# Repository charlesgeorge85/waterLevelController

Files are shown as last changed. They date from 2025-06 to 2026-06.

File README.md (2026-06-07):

# Water Level Controller for Home

This project implements a smart water tank pump controller using an ESP32 microcontroller. It manages the transfer of water between an Underground Tank (UGT) and an Overhead Tank (OHT), ensuring safe, efficient operation with dry-run protection and a web interface for monitoring and manual control.

## 1. Problem Statement

The system is designed to automatically control a water pump to transfer water from a UGT to an OHT. Key challenges addressed include:

- Preventing pump operation when UGT is empty (dry run).
- Automating pump ON/OFF based on OHT and UGT water levels.
- Providing manual mode, switch is set to manual, in manual mode, pump will be 'on', so thts pump can be controlled via main power switch

## 1.1 Tank Level Thresholds

- **Overhead Tank (OHT):**
  - `OHT_FULL`: Tank is full.
  - `OHT_EMPTY`: Tank is empty.

- **Underground Tank (UGT):**
  - `UGT_EMPTY`: Tank is empty.
  - `UGT_NOT_EMPTY`: Tank has sufficient water.

## 2. Use Cases

### 2.1 Pump Activation

The pump is activated when:
- OHT level is below `OHT_EMPTY`.
- UGT level is above `UGT_EMPTY`.

### 2.2 Pump Deactivation

The pump is turned off when:
- OHT reaches `OHT_FULL`, or
- UGT falls below `UGT_EMPTY`, or
- A dry-run condition is detected.

If deactivation is due to UGT low level, the pump will only reactivate once UGT is above `UGT_NOT_EMPTY`.

### 2.3 Dry Run Detection & Handling

- Dry-run is detected via motor current using a Current Transformer (CT).
- For a 0.25 HP motor, current < 0.8 A indicates a dry run, during normal run, the measured current is 1.27A
- On dry run:
  - A buzzer alerts.
  - Alarm can be cleared with a Alarm reset switch
  
## 3. Hardware Implementation

- **Controller**: ESP32
- **Features**:
  - Water level monitoring (UGT & OHT)
  - Motor control (auto/manual)
  - Current sensing
  - Configurable dry-run threshold
  - Web UI for (future Plan):
    - Displaying water levels
    - Manual motor control
    - Viewing current consumption
    - Threshold configuration

## 4. Web UI(future Plan)

A web-based interface hosted on ESP32 allows real-time visualization and control of the pump system.

## 5. ESP32 Devkit V1 details

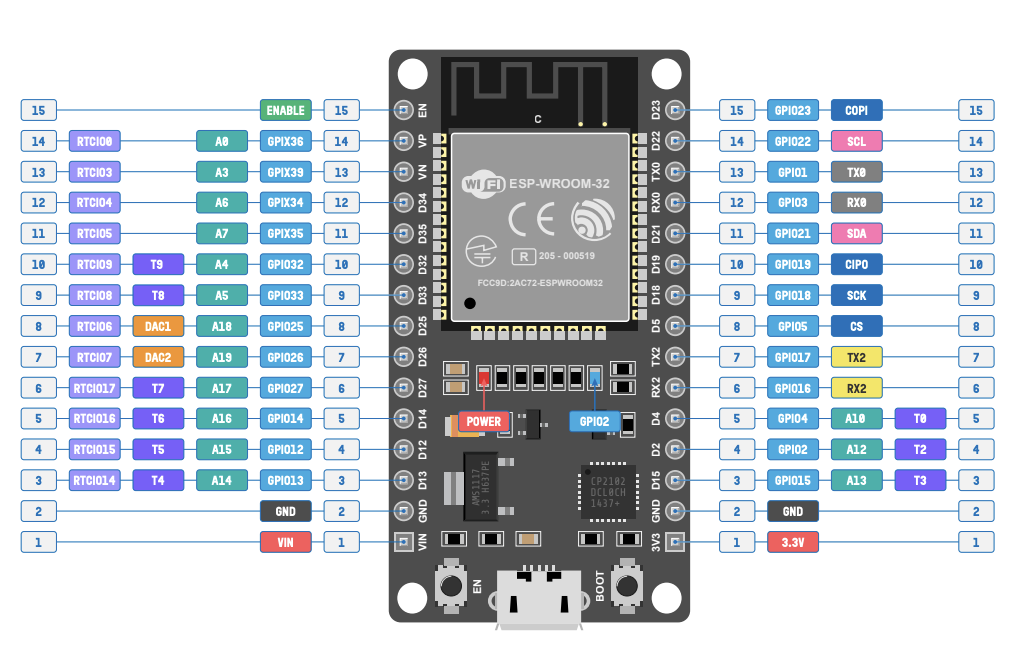
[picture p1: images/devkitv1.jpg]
ESP32 Pinout


[ESP32 DOIT DevKit V1 Board Details](https://www.espboards.dev/esp32/esp32doit-devkit-v1/)

---

### Author
Joseph George

### License
This project is open-source and available under the [MIT License](LICENSE).

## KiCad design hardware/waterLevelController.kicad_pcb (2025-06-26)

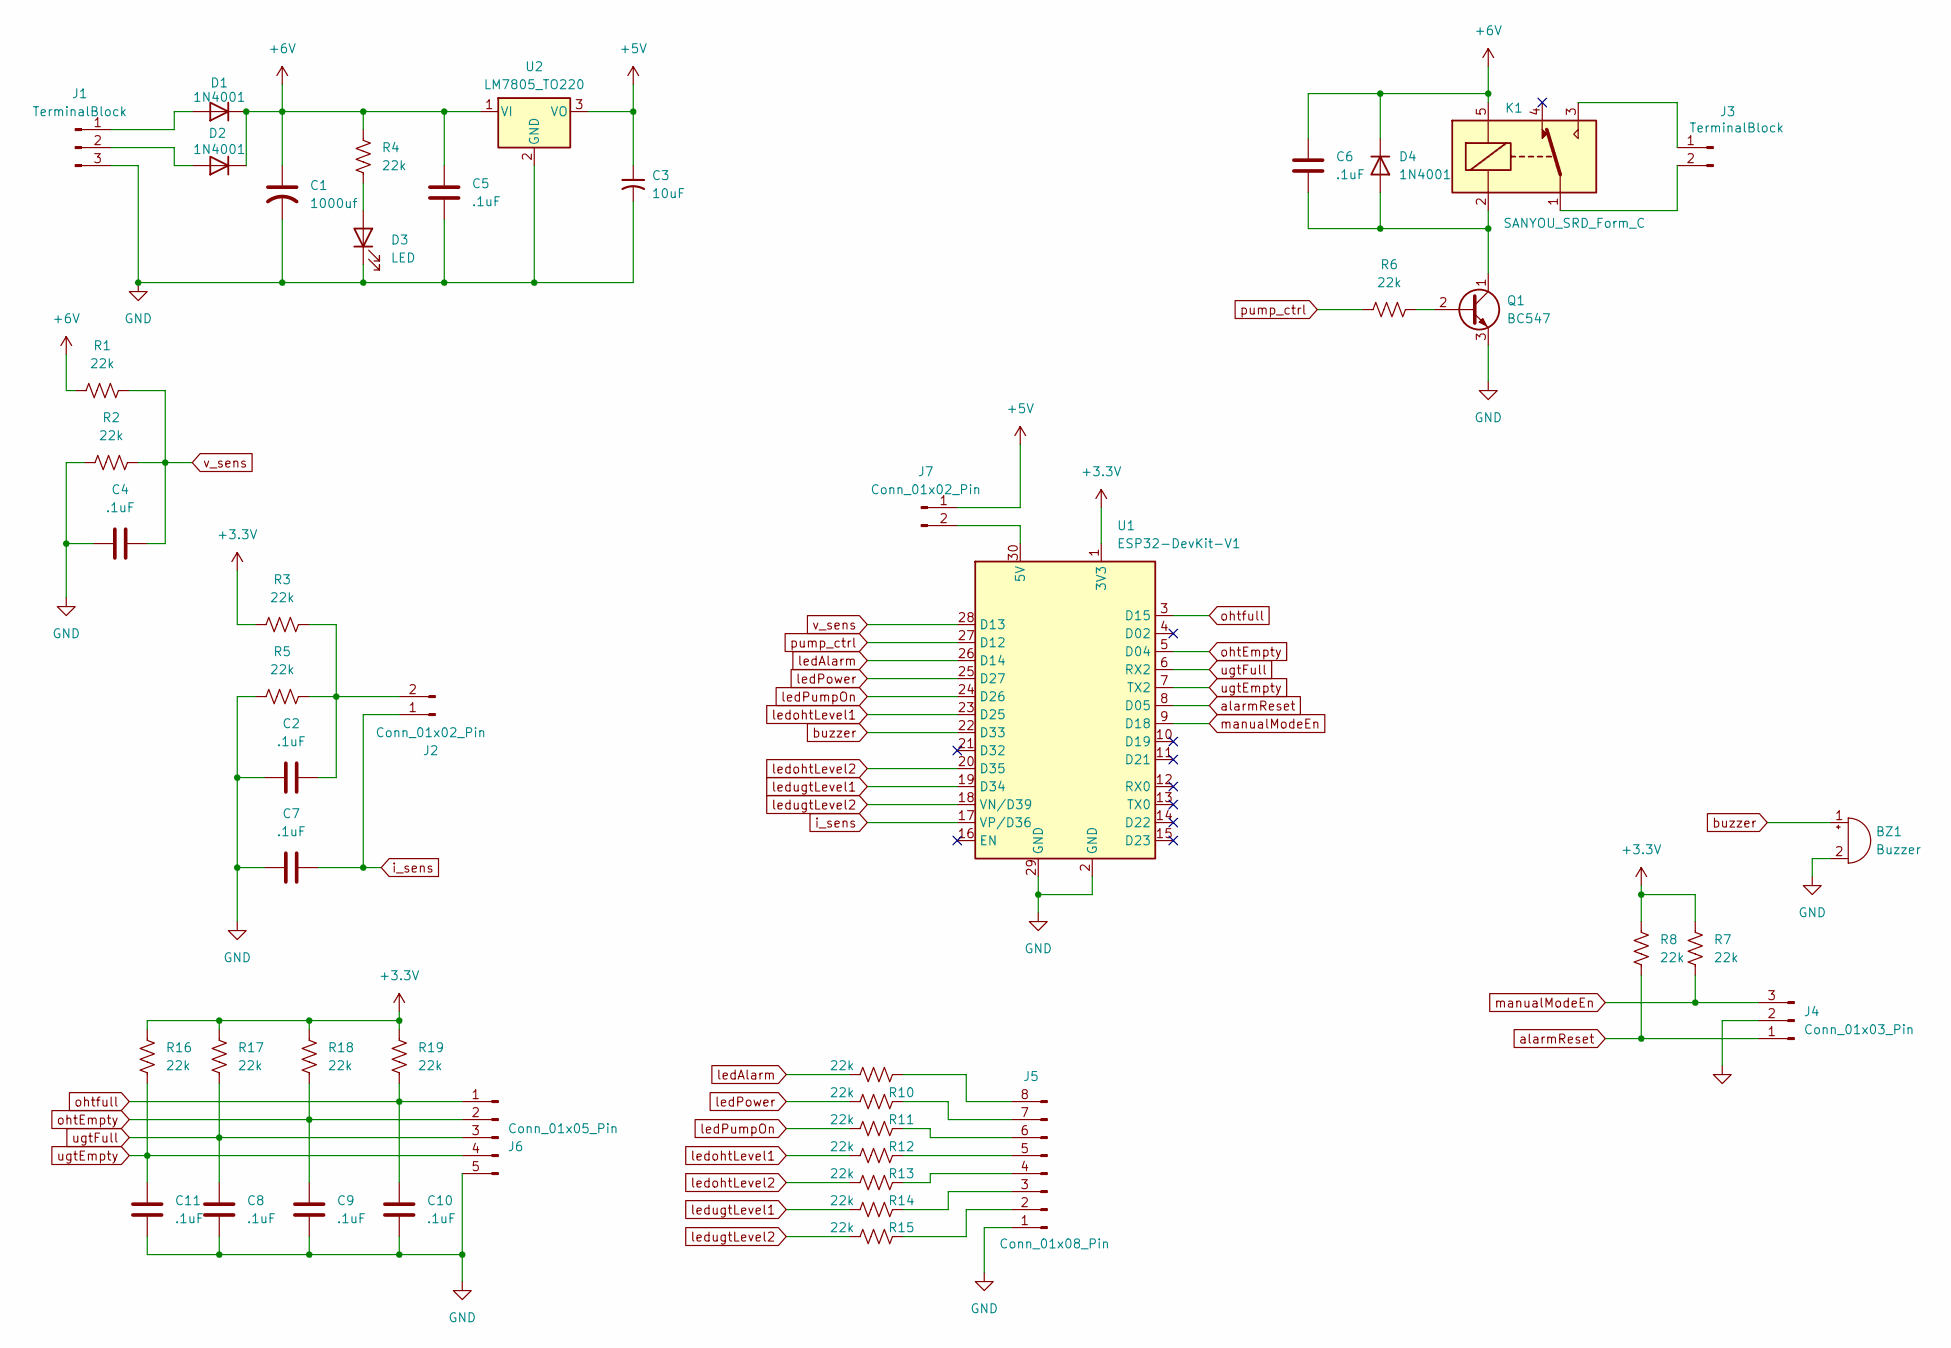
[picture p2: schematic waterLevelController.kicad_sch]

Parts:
BZ1: Buzzer; BUZ_12X7P6
C1: 1000uf; C_Radial_D12.5mm_H20.0mm_P5.00mm
C2, C4, C5, C6, C7, C8, C9, C10, C11: .1uF; C_Disc_D3.8mm_W2.6mm_P2.50mm
C3: 10uF; CP_Radial_D8.0mm_P2.50mm
D1, D2, D4: 1N4001; D_DO-41_SOD81_P10.16mm_Horizontal
D3: LED; LED_D3.0mm
J1: TerminalBlock; PhoenixContact_MCV_1,5_3-G-3.81_1x03_P3.81mm_Vertical
J2, J7: Conn_01x02_Pin; PinHeader_1x02_P2.54mm_Vertical
J3: TerminalBlock; PhoenixContact_MCV_1,5_2-G-3.81_1x02_P3.81mm_Vertical
J4: Conn_01x03_Pin; PinHeader_1x03_P2.54mm_Vertical
J5: Conn_01x08_Pin; PinHeader_1x08_P2.54mm_Vertical
J6: Conn_01x05_Pin; PhoenixContact_MCV_1,5_5-G-3.81_1x05_P3.81mm_Vertical
K1: SANYOU_SRD_Form_C; Relay_SPDT_SANYOU_SRD_Series_Form_C
Q1: BC547; TO-92_Wide
R1, R2, R3, R4, R5, R6, R7, R8, R9, R10, R11, R12, R13, R14, R15, R16, R17, R18, R19: 22k; R_Axial_DIN0309_L9.0mm_D3.2mm_P5.08mm_Vertical
U1: ESP32-DevKit-V1
U2: LM7805_TO220; TO-220-3_Vertical

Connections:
+3.3V: R3.1, R7.2, R8.2, R16.1, R17.1, R18.1, R19.1, U1.1 (3V3)
+5V: C3.1, J7.1, U2.3 (VO)
+6V: C1.1, C5.2, C6.2, D1.1 (K), D2.1 (K), D4.1 (K), K1.5, R1.1, R4.1, U2.1 (VI)
GND: BZ1.2 (-), C1.2, C2.1, C3.2, C4.1, C5.1, C7.1, C8.2, C9.2, C10.2, C11.2, D3.1 (K), J1.3, J4.2, J5.1, J6.5, Q1.3 (E), R2.1, R5.1, U1.2 (GND), U1.29 (GND), U2.2 (GND)
unnamed: D1.2 (A), J1.1
unnamed: D2.2 (A), J1.2
unnamed: D3.2 (A), R4.2
unnamed: C6.1, D4.2 (A), K1.2, Q1.1 (C)
unnamed: C2.2, J2.2, R3.2, R5.2
unnamed: J3.1, K1.3
unnamed: J3.2, K1.1
unnamed: J5.2, R15.1
unnamed: J5.3, R14.1
unnamed: J5.4, R13.1
unnamed: J5.5, R12.1
unnamed: J5.6, R11.1
unnamed: J5.7, R10.1
unnamed: J5.8, R9.1
unnamed: J7.2, U1.30 (5V)
unnamed: Q1.2 (B), R6.2
alarmReset: J4.1, R8.1, U1.8 (D05)
buzzer: BZ1.1 (+), U1.22 (D33)
i_sens: C7.2, J2.1, U1.17 (VP/D36)
ledAlarm: R9.2, U1.26 (D14)
ledPower: R10.2, U1.25 (D27)
ledPumpOn: R11.2, U1.24 (D26)
ledohtLevel1: R12.2, U1.23 (D25)
ledohtLevel2: R13.2, U1.20 (D35)
ledugtLevel1: R14.2, U1.19 (D34)
ledugtLevel2: R15.2, U1.18 (VN/D39)
manualModeEn: J4.3, R7.1, U1.9 (D18)
ohtEmpty: C9.1, J6.2, R18.2, U1.5 (D04)
ohtfull: C10.1, J6.1, R19.2, U1.3 (D15)
pump_ctrl: R6.1, U1.27 (D12)
ugtEmpty: C11.1, J6.4, R16.2, U1.7 (TX2)
ugtFull: C8.1, J6.3, R17.2, U1.6 (RX2)
v_sens: C4.2, R1.2, R2.2, U1.28 (D13)

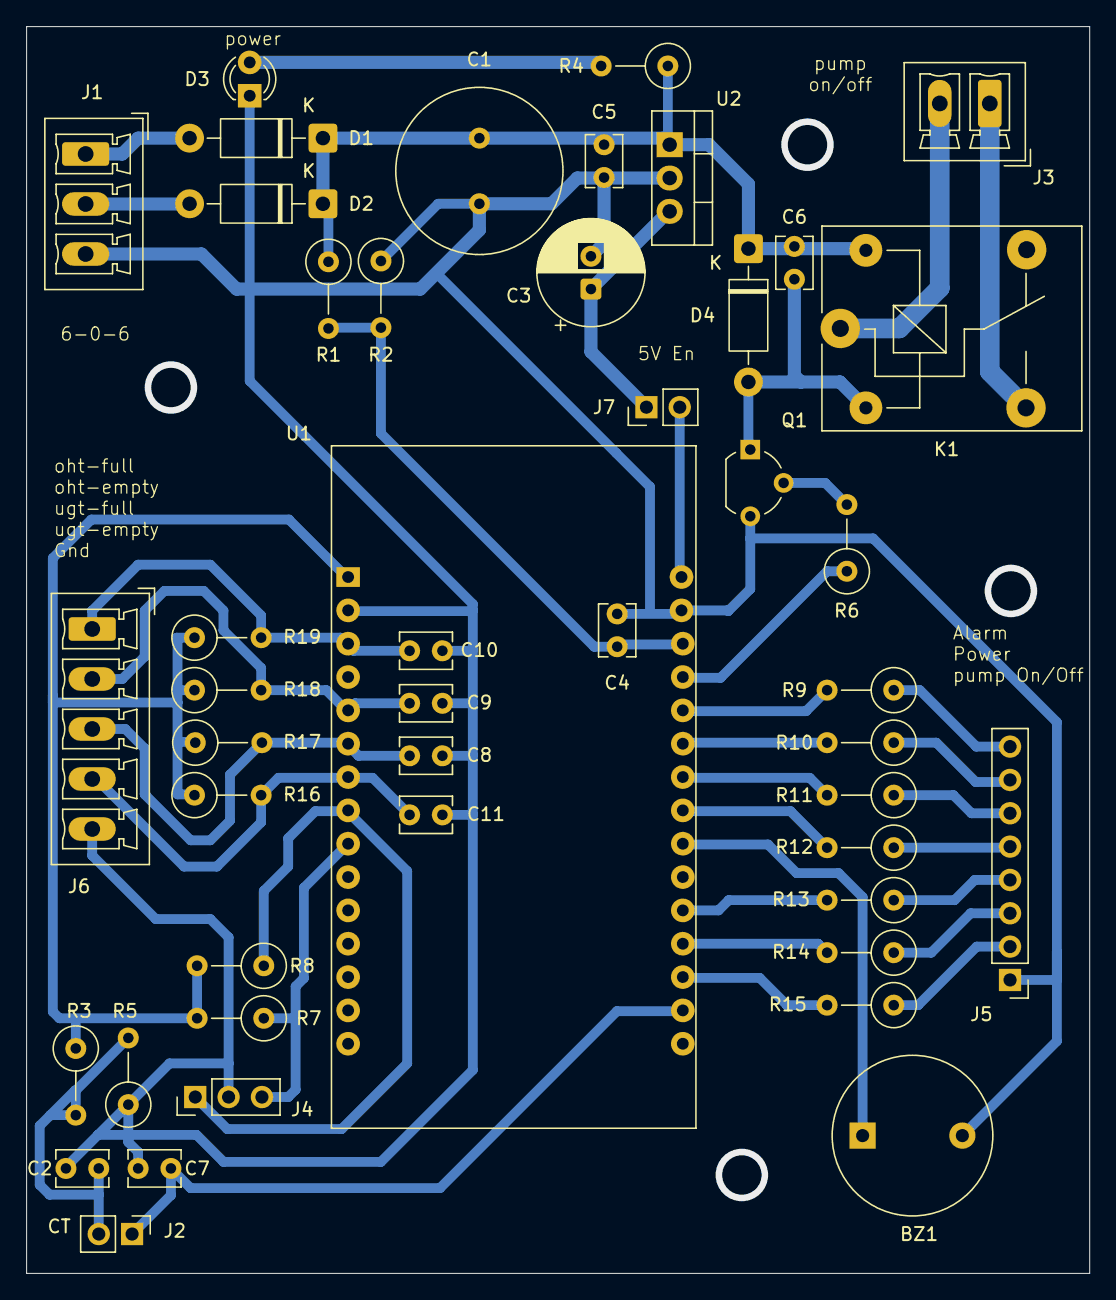
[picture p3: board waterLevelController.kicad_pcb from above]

Board: 2 copper layers, 81.0 x 95.0 mm, 46 parts (0 on the bottom side), 37 nets.

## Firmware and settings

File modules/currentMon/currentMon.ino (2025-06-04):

#define ADC_PIN 36          // ESP32 ADC pin (GPIO36 = ADC1_CH0)
#define VREF 3.3            // ADC reference voltage
#define ADC_RES 4095        // 12-bit ADC
#define VOLTAGE_BIAS 1.580  // Measured midpoint voltage (bias)
#define SENSOR_SENSITIVITY 0.1  // 0.1 V/A (for SCT-013-010)
#define SAMPLE_DURATION 200  // Sampling time in milliseconds (for 10 cycles at 50Hz)

void setup() {
  Serial.begin(115200);
  analogReadResolution(12);  // ESP32 default is 12-bit
}

void loop() {
  unsigned long i_sam_start_time = millis();
  float sum_squared = 0;
  int sample_count = 0;

  while ((millis() - i_sam_start_time) < SAMPLE_DURATION) {
    int adc_val = analogRead(ADC_PIN);
    float voltage = (adc_val * VREF) / ADC_RES;
    float ac_component = voltage - VOLTAGE_BIAS;

    sum_squared += ac_component * ac_component;
    sample_count++;

    delayMicroseconds(200); // ~5 kHz sampling
  }

  // Calculate RMS voltage
  float mean_squared = sum_squared / sample_count;
  float rms_voltage = sqrt(mean_squared);

  // Convert to current using sensor sensitivity
  float rms_current = rms_voltage / SENSOR_SENSITIVITY;

  //scaling Correction, bu board 
  rms_current *= 0.258/3.34;

  Serial.print("RMS Current = ");
  Serial.print(rms_current, 3);
  Serial.println(" A");

  delay(1000); // Wait before next reading
}

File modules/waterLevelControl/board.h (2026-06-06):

#ifndef BOARD_H
#define BOARD_H

// GPIO Pin Definitions
#define OHT_FULL_PIN        15
#define OHT_EMPTY_PIN       04
#define UGT_NOT_EMPTY_PIN   16
#define UGT_EMPTY_PIN       17

#define ALARM_CLEAR_PIN     05
#define MANUAL_MODE_SWITCH  18

#define PUMP_CONTROL_PIN    32
#define PUMP_LED_PIN        02
#define BUZZER_PIN          33

// Status LEDs
#define LED_ALRM_PIN        27
#define LED_PUMP_PIN        26
#define LED_PWR_PIN         14

// ADC Parameters
#define VREF 3.3
#define ADC_RES 4095

// Current sense
#define CT_SENS_PIN 36

#define VOLTAGE_BIAS 1.580
#define SENSOR_SENSITIVITY 0.1
#define SAMPLE_DURATION 200

// Dry-run thresholds
#define DRY_RUN_CURRENT_THRESHOLD   0.8
#define DRY_RUN_RECOVERY_THRESHOLD  2.5

// Voltage Sense
#define VAC_SENS_ADC_PIN 13

// Dry-run delay before checking (after pump ON)
const unsigned long DRY_RUN_DELAY_MS = 0.5 * 60 * 1000;
const unsigned long DRY_RUN_BUZZ_INTERVAL = 30 * 60 * 1000;

#endif

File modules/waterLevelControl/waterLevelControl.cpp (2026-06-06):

#include <Arduino.h>
#include "board.h"

// System States
bool toggle = false;
bool pumpOn = false;
bool manualMode = false;
bool dryRunDetected = false;
bool ugtPreviouslyEmpty = false;
bool ohtPreviouslyEmpty = false;

unsigned long lastDryRunBuzzTime = 0;
unsigned long pumpStartTime = 0;

void setup() {
  Serial.begin(115200);
  analogReadResolution(12);  // ESP32 default is 12-bit
  
  // Sensor Inputs
  pinMode(OHT_FULL_PIN, INPUT);
  pinMode(OHT_EMPTY_PIN, INPUT);
  pinMode(UGT_EMPTY_PIN, INPUT);
  pinMode(UGT_NOT_EMPTY_PIN, INPUT);

  // Control Outputs
  pinMode(PUMP_CONTROL_PIN, OUTPUT);
  pinMode(PUMP_LED_PIN, OUTPUT);
  pinMode(BUZZER_PIN, OUTPUT);

  pinMode(LED_ALRM_PIN, OUTPUT);
  pinMode(LED_PUMP_PIN, OUTPUT);
  pinMode(LED_PWR_PIN, OUTPUT);

  // User Inputs
  pinMode(ALARM_CLEAR_PIN, INPUT_PULLUP);
  pinMode(MANUAL_MODE_SWITCH, INPUT_PULLUP);

  digitalWrite(PUMP_CONTROL_PIN, LOW);
  digitalWrite(PUMP_LED_PIN, LOW);
  digitalWrite(BUZZER_PIN, LOW);
  
  digitalWrite(LED_ALRM_PIN, LOW);
  digitalWrite(LED_PUMP_PIN, LOW);
  digitalWrite(LED_PWR_PIN, LOW);


}

bool readSensor(int pin) {
  return digitalRead(pin) == LOW; // Assume LOW means "active"
}

void activatePump() {
  if (!pumpOn) {
    digitalWrite(PUMP_CONTROL_PIN, HIGH);
    digitalWrite(PUMP_LED_PIN, HIGH);
    digitalWrite(LED_PUMP_PIN, HIGH);
    pumpOn = true;
    pumpStartTime = millis();
    tone(BUZZER_PIN, 440, 300); // 300 ms sec beep @440Hz
    Serial.println("Pump ON");
  }
}

void deactivatePump() {
  if (pumpOn) {
    digitalWrite(PUMP_CONTROL_PIN, LOW);
    digitalWrite(PUMP_LED_PIN, LOW);
    digitalWrite(LED_PUMP_PIN, LOW);
    pumpOn = false;
    Serial.println("Pump OFF");
    tone(BUZZER_PIN, 2000, 200); // 300 ms sec beep @440Hz
    
  }
}

void handleDryRun(float current) {
  if (!pumpOn and !dryRunDetected) return; // ✅ Only check if pump is running

  unsigned long now = millis();
  if (now - pumpStartTime < DRY_RUN_DELAY_MS) {
    // ✅ Wait 2 minutes before checking
    return;
  }
   Serial.println("Dry run check initiated...");
 
 if (current < DRY_RUN_CURRENT_THRESHOLD) {
      dryRunDetected = true;
      deactivatePump();
      Serial.println("Dry run detected.....");
    }

  if (dryRunDetected) {
    
      tone(BUZZER_PIN, 1000, 100); // 0.1 sec beep @ 1KHz
      digitalWrite(LED_ALRM_PIN, toggle);
    

    if (digitalRead(ALARM_CLEAR_PIN) == LOW) {
      dryRunDetected = false;
      Serial.println("Dry-run alarm cleared.");
      digitalWrite(LED_ALRM_PIN, LOW);
    }
  }
}


float voltMon()
{
 // Voltage Sampling
  int adc_val = analogRead(VAC_SENS_ADC_PIN); // 0 to 4095
  float voltageSense = (adc_val / 4095.0) * 3.3; // Convert to volts
  //scaling correction by board measurement
  float voltMains = 242*voltageSense/2.98;
  return voltMains;
}

float currentMon()
{
  // Current Sampling
  unsigned long i_sam_start_time = millis();
  float sum_squared = 0;
  int sample_count = 0;

  while ((millis() - i_sam_start_time) < SAMPLE_DURATION) {
    int adc_val = analogRead(CT_SENS_PIN);
    float voltage = (adc_val * VREF) / ADC_RES;
    float ac_component = voltage - VOLTAGE_BIAS;

    sum_squared += ac_component * ac_component;
    sample_count++;

    delayMicroseconds(200); // ~5 kHz sampling
  }

  // Calculate RMS voltage
  float mean_squared = sum_squared / sample_count;
  float rms_voltage = sqrt(mean_squared);

  // Convert to current using sensor sensitivity
  float rms_current = rms_voltage / SENSOR_SENSITIVITY;

  //scaling Correction, bu board 
  rms_current *= 0.258/3.34;

  return(rms_current);
}

void loop() {
  
  float rms_current = currentMon();
  float rms_voltage = voltMon();
  float power = rms_voltage * rms_current;
  
  /*
  Serial.print("RMS Current = ");
  Serial.print(rms_current, 3);
  Serial.println(" A");
  
  Serial.print("Vrms = ");
  Serial.print(rms_voltage, 3);
  Serial.println(" V");

  Serial.print("Power = ");
  Serial.print(power, 3);
  Serial.println(" Watts");
*/
  manualMode = digitalRead(MANUAL_MODE_SWITCH) == LOW;
  toggle = !toggle;

  
  //digitalWrite(LED_ALRM_PIN, toggle);
  digitalWrite(LED_PWR_PIN, HIGH);
  
  if (manualMode) {
    Serial.println("Manual Mode Active");
    // Optionally handle pump ON/OFF via buttons here
    activatePump();
  } else {
    
    // Read tank sensor states
    bool ohtEmpty = digitalRead(OHT_EMPTY_PIN) == HIGH;
    bool ohtFull = digitalRead(OHT_FULL_PIN) == LOW;
    bool ugtEmpty = digitalRead(UGT_EMPTY_PIN) == HIGH;
    bool ugtNotEmpty = digitalRead(UGT_NOT_EMPTY_PIN) == LOW;
/*
    Serial.printf("ohtEmpty: %s\n", ohtEmpty ? "true" : "false");  // Outputs: Status: true
    Serial.printf("ohtFull: %s\n", ohtFull ? "true" : "false");  // Outputs: Status: true
    Serial.printf("ugtEmpty: %s\n", ugtEmpty ? "true" : "false");  // Outputs: Status: true
    Serial.printf("ugtNotEmpty: %s\n", ugtNotEmpty ? "true" : "false");  // Outputs: Status: true
*/
    // Track UGT history
    if (ugtEmpty) {
      ugtPreviouslyEmpty = true;
      deactivatePump(); // Safety: prevent dry run
    }

    if (ugtPreviouslyEmpty && ugtNotEmpty && !ugtEmpty) {
      ugtPreviouslyEmpty = false; // Reset lock
    }

    // Track OHT History

    if (ohtEmpty) {
      ohtPreviouslyEmpty = true;
    }

    if (ohtPreviouslyEmpty && ohtFull && !ohtEmpty) {
      ohtPreviouslyEmpty = false; // Reset lock
    }

    // Normal operation
    if (!manualMode && !dryRunDetected && !ugtPreviouslyEmpty) {
      if (ohtPreviouslyEmpty && !ugtEmpty ) {
        activatePump();
      } else {
        deactivatePump();
      }
    } else {
      deactivatePump();
    }
  }

  // Dry run check (only if pump is ON & delay passed)
  handleDryRun(rms_current);

  delay(1000);
}

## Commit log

2025-06-03 board level sensor validated
2025-06-04 Voltage and Current monitor intergrated in main files
2025-06-04 unwanted print removed
2025-06-24 Add files via upload
    These are the hardware design files
    [waterLevelController.kicad_pcb, waterLevelController.kicad_sch]
2025-06-24 Gerber generated Version
    [waterLevelController.kicad_pcb, waterLevelController.kicad_sch]
2025-06-26 silkscreen updated
    [waterLevelController.kicad_pcb]
2026-06-06 Convert to PlatformIO C++ project and centralize board configuration
2026-06-07 Update README.md
    esp32 board details added
